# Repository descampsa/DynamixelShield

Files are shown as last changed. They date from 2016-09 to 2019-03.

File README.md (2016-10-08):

# Dynamixel shield

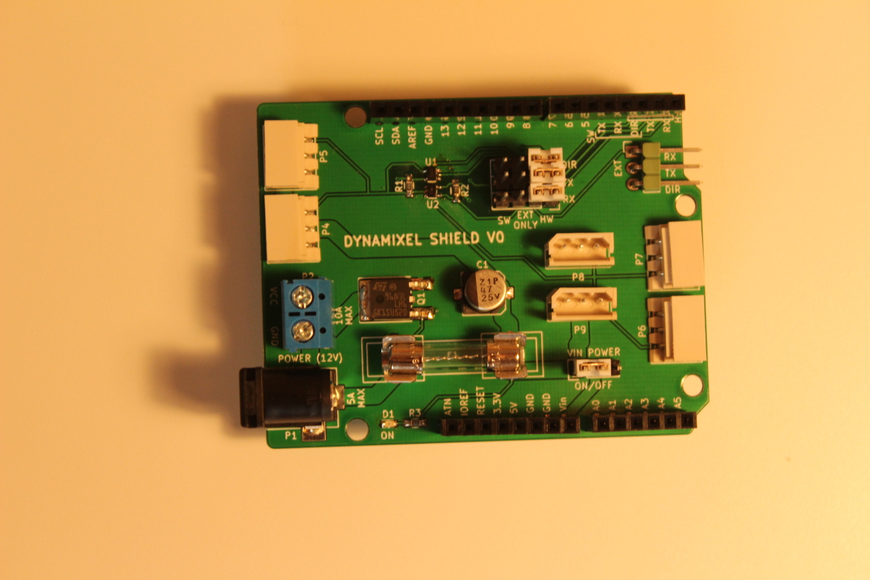
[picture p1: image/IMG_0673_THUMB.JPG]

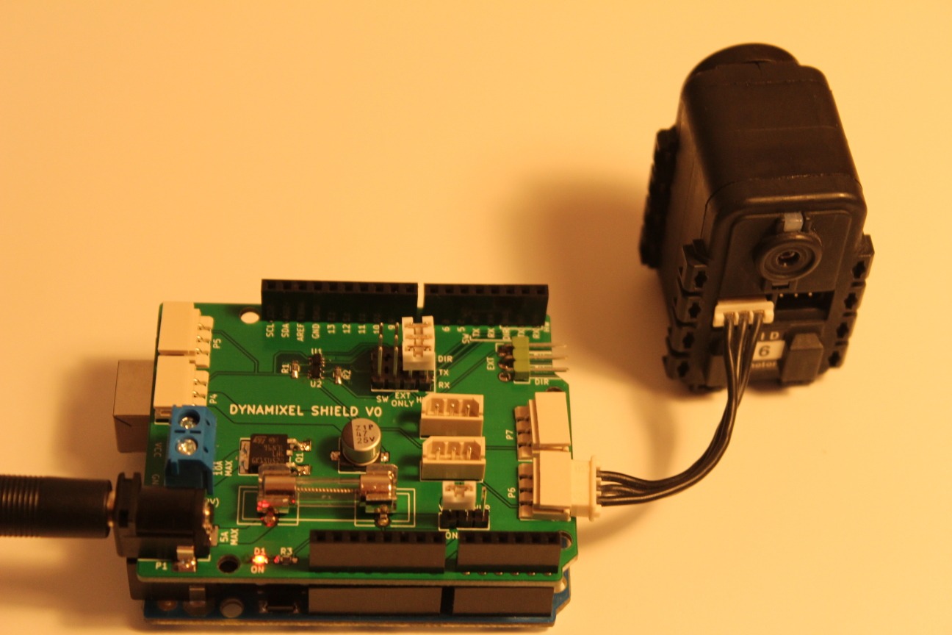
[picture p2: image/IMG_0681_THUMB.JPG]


## What is it?

This is an arduino shield to control dynamixel servo motors from Robotis. AX and MX series (TTL version) are supported. Thanks to their half-duplex serial control protocol, you can chain them and control a lot of motor simultaneously (up to 254 in theory). It is possible to control those motors with an arduino without additionnal hardware, but this board makes it easier and cleaner.

## How to use it?

### Hello world (aka blink my led)

First install the [ardyno](https://github.com/descampsa/ardyno/) library, using the Arduino Library Manager, or directly from the github repository.
Then open the "test_led" example and upload it. The shield can not be installed when you install the program.
Install the shield, check that the jumpers are on 'HW' position, connect the motor and a 12v power supply, and voila, the motor "led" should start blinking!
To get the motor moving (that's the point, after all), check the "test_motor" exemple. The documentation is still lacking, but by browsing examples and code, you should be able to do understand how it works. If you have any question, just ask.

### Software serial

The default mode explained above is to use the first hardware UART (Serial) of the board to communicate with the motors. This has the advantage that you can usethe full communication speed (up to 2Mbaud, by default 1Mbaud) of the protocol. However, boards that only have one hardaware uart (e.g. Uno), that means that you can't simultaneously use the USB port to communicate with the external world, since it also uses this UART. If you want to do that, you have to use the SoftwareSerial mode. The disadvantage is that you are limited to low baud rates (check the SoftwareSerial library documentation). You will have to change the baud rate of the motor using the hardware serial before (see "test_speed" example).

To use the SoftwareSerial mode, change the jumper to 'SW' position, and replace the line
```
HardwareDynamixelInterface interface(Serial,2);
```
by

```
SoftwareDynamixelInterface interface(4,3,2);
```

The first version take the hardware serial instance, and the direction pin as parameters, while the second one take rx pin, tx pin and direction pin.

### Other Hardware Serial

For boards that have multiple hardware uart, you may use any of those ports by connecting the corresponding pins to the 'EXT' connector. Just set the jumper to 'EXT ONLY' position, and connect RX/TX/DIR pins to the rx/tx pins of the uart and the direction pin configured in your code.

## Which boards are compatible?

Most of the code is platform independent, but it has only been tested with AVR boards. If you want to use another platform and find a bug, open an issue in ardyno repository.
The shield supports both 5V and 3.3V boards.

I also successfully tested it with the Arduino 101, but there are still a few shortcomings in the serial libray of this board, so this is experimental.

## Great, how do i get one?

The good news is that all is open source, the kicad project, gerber file, code, bom, all you need to make your own. Gerber and bom are also available on [kitnic](kitnic.it), where you may order the parts very easily. The bad news is that you can't buy one, i do not sell it for now.
I have a few unpopulated pcb left, however, so if you are interested, just ask and i will send you one for shipping cost.

## Warning

This board is functionnal, but has not yet been tested extensively, especially for high loads. Make sure you know what you are doing if you use it.

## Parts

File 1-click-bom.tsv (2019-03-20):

References | Qty | Description | Manufacturer | MPN | Digikey | Mouser | RS | Newark | Farnell
Q1 | 1 | MOSFET N TO-252-2Lead | ON semiconductor | NTD4904NT4G | NTD4904NT4GOSCT-ND | 863NTD4904NT4G
F1 | 2 | F Small Fuse Fuseholder5x20 horiz lateral | Littelfuse | 01110501Z | F4189-ND | 57601110501Z |  | 69R7705 | 1848686
F1_10A | 1 | Fuse 5x20 10A | Littelfuse | 5ST 10-R | 507-1256-ND | 5305ST10R
F1_5A | 1 | Fuse 5x20 5A | Littelfuse | 5ST 5-R | 507-1253-ND | 5305ST5R
P1 | 1 | BARREL JACK DC Barrel Jack | CUI Inc. | PJ-102AH | CP-102AH-ND | 490PJ102AH
P2 | 1 | CONN 01X02 Connector 01x02 bornier2 5.08mm | TE Connectivity | 1776493-2 | A122765-ND | 57117764932 |  | 95Y9029
U1 | 1 | 74AHCT1G126 SOT-353 | Diodes Incorporated | 74AHCT1G126SE-7 | 74AHCT1G126SE-7DICT-ND | 62174AHCT1G126SE7 |  |  | 2057393
U2 | 1 | 74AHC1G125 SOT-353 | Diodes Incorporated | 74AHC1G125SE-7 | 74AHC1G125SE-7DICT-ND | 62174AHC1G125SE7 |  | 47T3881 | 1893809
C1,C2 | 1 | CP 220uF Polarised capacitor c elec 6.3x7.7 25V 20% | Panasonic | EEE-FTE221XAP | PCE5009CT-ND | 667EEEFTE221XAP |  | 29AC5209 | 2284803
R1,R2,R3,R4,R6 | 5 | R 10K Resistor 0603 | Panasonic | ERJ-3GEYJ103V | P10KGDKR-ND | 667ERJ3GEYJ103V | 7325656 | 97W7470 | 2059627
R5 | 1 | R 200 Resistor 0603 | Panasonic | ERJ-3GEYJ201V | P200GCT-ND | 667ERJ3GEYJ201V | 7325769 | 65T8597 | 2059582
D1 | 1 | LED 0603 Red | OSRAM Opto Semiconductors | LS Q976-NR-1 | 475-2512-1-ND | 720LSQ976NR1
P3 | 1 | CONN 01X03 Connector 01x03 Pin Header Angled 1x03 2.54mm | Molex | 22-28-8030 | WM50013-03-ND | 53822288030 |  | 91M6511
P4,P5,P6,P7 | 4 | CONN 01X03 Connector 01x03 Molex spox 1x3 right 2.5mm | Molex | 22-05-7035 | WM18901-ND | 53822057035 | 6878095 | 57R9151
P8,P9 | 2 | CONN 01X03 Connector 01x03 Molex spox 1x3 straight 2.5mm | Molex | 22-03-5035 | WM18887-ND | 53822035035 | 6878048 | 98K6552 | 9979620
JP1,JP2,JP3 | 3 | JUMPER4 Pin Header Straight 1x04 2.54mm | Molex | 22-28-4030 | WM50014-03-ND | 53822284030 |  | 56H1960
JP4 | 1 | JUMPER3 Pin Header Straight 1x03 2.54mm | Molex | 22-28-4040 | WM50014-04-ND | 53822284040 |  | 29X1962 | 2381172
JP1_,JP2_,JP3_,JP4_ | 4 | SHUNT 1x2 2.54mm | Amphenol FCI | 68786-102LF | 609-3121-ND | 64968786102LF |  | 53K1469 | 2579771
SHIELD1 | 1 | Arduino Shield stacking headers for Arduino (R3 Compatible) | Adafruit |  | 1528-1074-ND | 48585

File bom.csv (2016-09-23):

DYNAMIXEL_SHIELD
N° Mouser | N° de fab. | Fabricant | Description | RoHS | Cycle de vie | Qté. | Prix (EUR) | Poste: (EUR)
511-STD96N3LLH6 | STD96N3LLH6 | STMicroelectronics | MOSFET N-Ch 30V 0.0037 Ohm 80A STripFET VI | RoHS : conforme |  | 1 | € 0,679 | € 0,68
621-74AHCT1G126SE-7 | 74AHCT1G126SE-7 | Diodes Incorporated | Tampons et circuits d’excitation AHC TTL Compatible LOGIC | RoHS : conforme |  | 1 | € 0,22 | € 0,22
621-74AHC1G125SE-7 | 74AHC1G125SE-7 | Diodes Incorporated | Tampons et circuits d’excitation SINGLE NON INVERTING DRIVER 3-STATE | RoHS : conforme |  | 1 | € 0,256 | € 0,26
576-01110501Z | 01110501Z | Littelfuse | Mâchoires ACS 2AG PC MNT CLIP | RoHS : conforme |  | 2 | € 0,109 | € 0,22
530-5ST10-R | 5ST 10-R | Bel | Fusibles à cartouche Fuse | RoHS : conforme |  | 1 | € 0,192 | € 0,19
538-22-03-5035 | 22-03-5035 | Molex | Embases et logements de câbles 2.5 VERT HDR SPOX 3P shrouded | RoHS : conforme |  | 2 | € 0,443 | € 0,89
538-22-05-7035 | 22-05-7035 | Molex | Embases et logements de câbles 3 CKT 2.5MM R/A HDR | RoHS : conforme |  | 4 | € 0,471 | € 1,88
490-PJ-102AH | PJ-102AH | CUI Inc. | Connecteurs d'alimentation continue Power Jacks | RoHS : conforme | Nouveau chez Mouser | 1 | € 1,08 | € 1,08
667-ERJ-3GEYJ103V | ERJ-3GEYJ103V | Panasonic | Résistances à couches épaisses - CMS 0603 10Kohms 5% AEC-Q200 | Conforme à RoHS par dispense |  | 3 | € 0,091 | € 0,27
630-HSMC-C130 | HSMC-C130 | Broadcom Limited | DEL standard - CMS Red Thin Profile 155lm | RoHS : conforme |  | 1 | € 0,08 | € 0,08
649-68786-102LF | 68786-102LF | FCI / Amphenol | Embases et logements de câbles SHUNT 15u" GOLD | RoHS : conforme |  | 4 | € 0,172 | € 0,69
485-85 | 85 | Adafruit | Accessoires Adafruit Shield stacking headers for Arduino (R3 Compatible) | RoHS : conforme |  | 1 | € 1,76 | € 1,76
571-1776493-2 | 1776493-2 | TE Connectivity | Borniers fixes SIDE WIRE ENTRY TB 5.08MM BL | RoHS : conforme |  | 1 | € 0,31 | € 0,31
530-5VT5-R | 5VT 5 -R | Bel | Fusibles à cartouche | RoHS : conforme |  | 1 | € 0,183 | € 0,18
647-UWT1E470MCL6S | UWT1E470MCL6GS | Nichicon | Condensateurs électrolytiques en aluminium - CMS 25volts 47uF 6.3x5.8 20% | RoHS : conforme |  | 1 | € 0,284 | € 0,28
571-826947-3 | 826947-3 | TE Connectivity | Embases et logements de câbles 2X03 POS VERT TIN | RoHS : conforme |  | 1 | € 0,188 | € 0,19
571-4-103321-5 | 4-103321-5 | TE Connectivity | Embases et logements de câbles 03 MODII HDR SRST B/A .100CL | RoHS : conforme |  | 1 | € 0,094 | € 0,09
571-5-146274-4 | 5-146274-4 | TE Connectivity | Embases et logements de câbles 4P HEADER TIN single row | RoHS : conforme |  | 3 | € 0,16 | € 0,48

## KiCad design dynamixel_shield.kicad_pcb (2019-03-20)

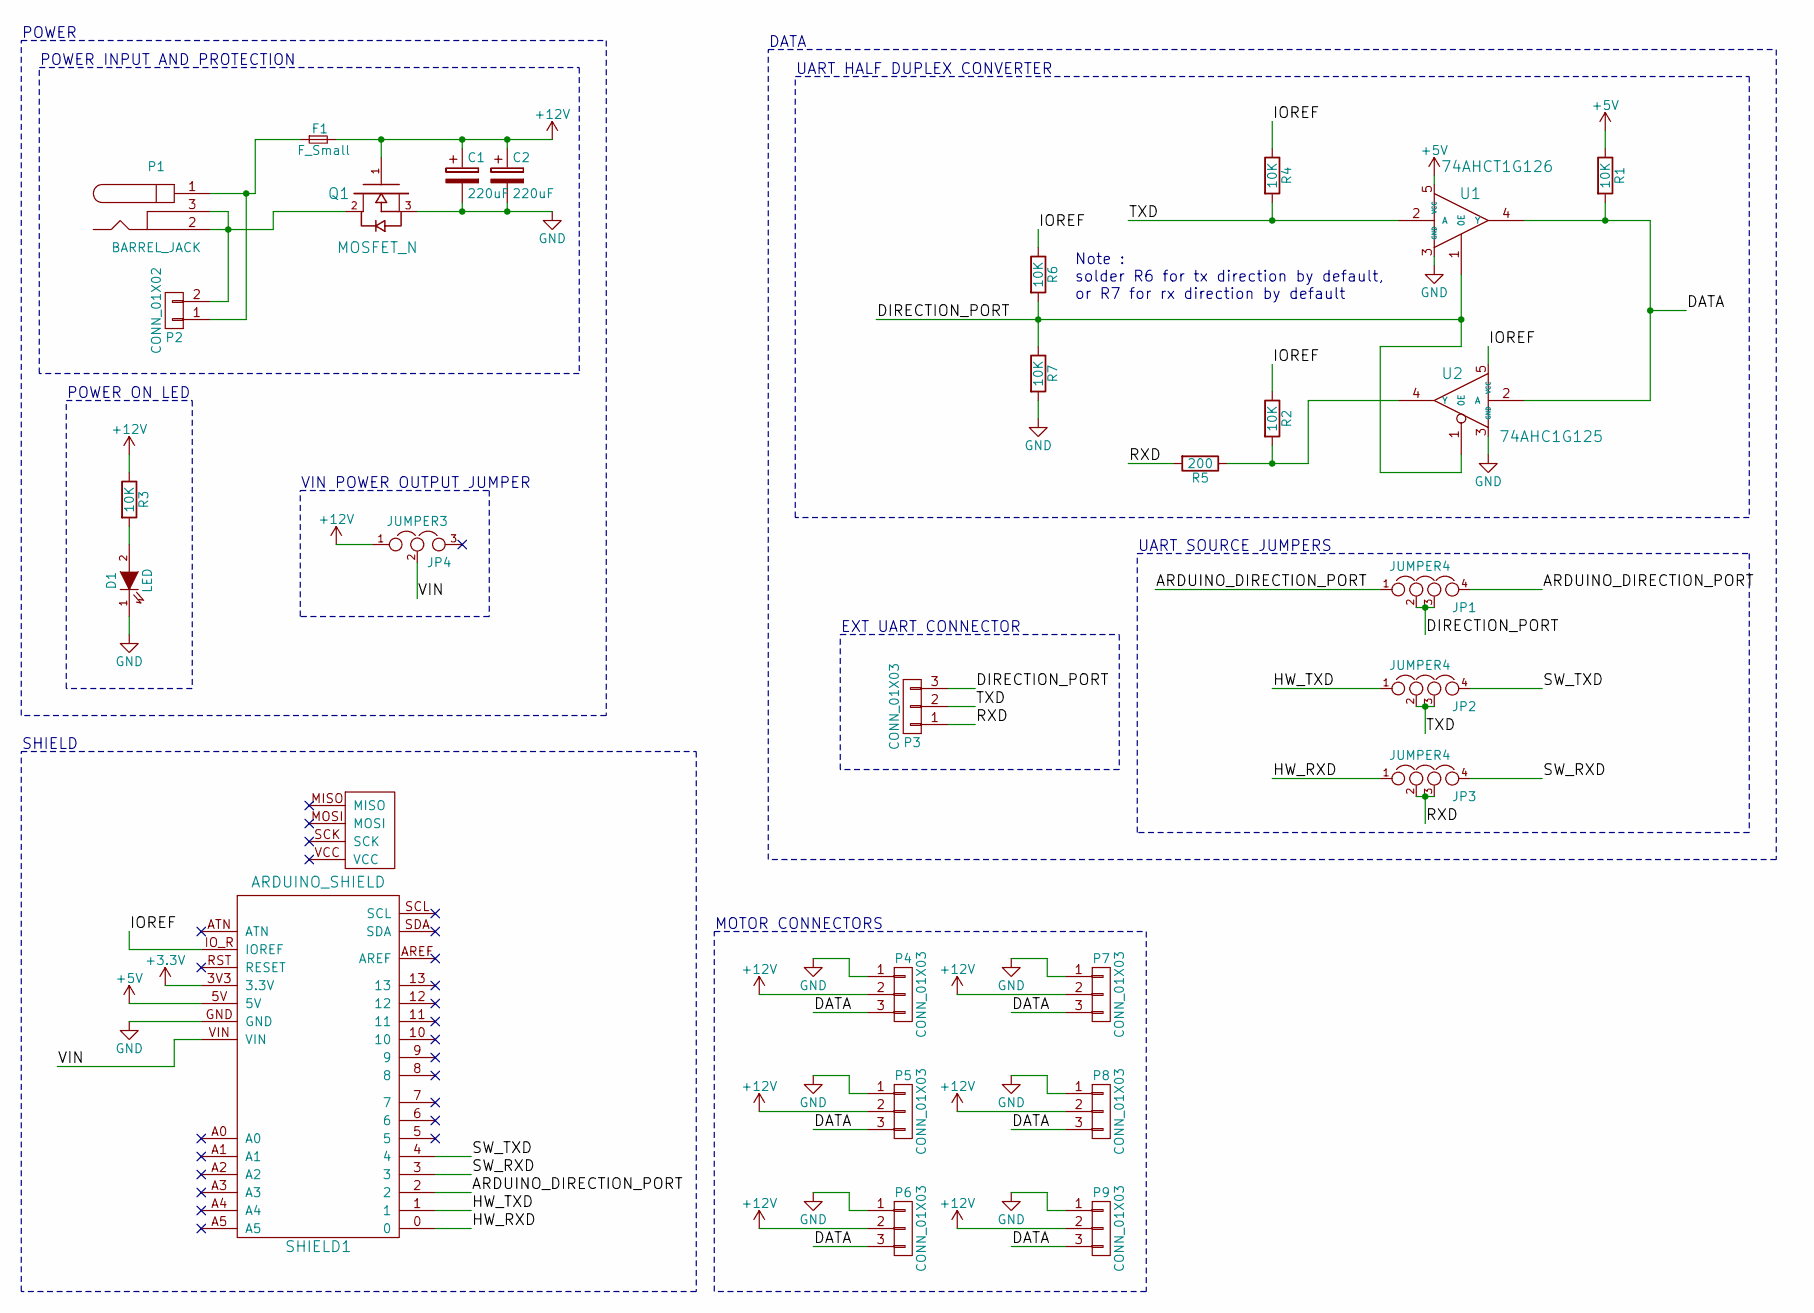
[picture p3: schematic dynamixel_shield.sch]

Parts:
C1, C2: 220uF; CP_Elec_6.3x7.7
D1: LED; LED_0603
F1: F_Small; Fuseholder5x20_horiz_lateral
JP1, JP2, JP3: JUMPER4; Pin_Header_Straight_1x04
JP4: JUMPER3; Pin_Header_Straight_1x03
P1: BARREL_JACK
P2: CONN_01X02; bornier2
P3: CONN_01X03; Pin_Header_Angled_1x03
P4, P5, P6, P7: CONN_01X03; Molex_spox_1x3_right
P8, P9: CONN_01X03; Molex_spox_1x3_straight
Q1: MOSFET_N; TO-252-2Lead
R1, R2, R3, R4, R6, R7: 10K; R_0603_HandSoldering
R5: 200; R_0603_HandSoldering
SHIELD1: ARDUINO_SHIELD; Arduino_shield_dynamixel
U1: 74AHCT1G126; SOT-353
U2: 74AHC1G125; SOT-353

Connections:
+3V3: SHIELD1.3V3 (3.3V)
+5V: R1.1, SHIELD1.5V, U1.5 (VCC)
+12V: C1.1, C2.1, F1.2, JP4.1, P4.2, P5.2, P6.2, P7.2, P8.2, P9.2, Q1.1 (G), R3.1
/ARDUINO_DIRECTION_PORT: JP1.1, JP1.4, SHIELD1.2
/DATA: P4.3, P5.3, P6.3, P7.3, P8.3, P9.3, R1.2, U1.4 (Y), U2.2 (A)
/DIRECTION_PORT: JP1.2, JP1.3, P3.3, R6.2, R7.1, U1.1 (0E), U2.1 (0E)
/HW_RXD: JP3.1, SHIELD1.0
/HW_TXD: JP2.1, SHIELD1.1
/IOREF: R2.1, R4.1, R6.1, SHIELD1.IO_R (IOREF), U2.5 (VCC)
/RXD: JP3.2, JP3.3, P3.1, R5.2
/SW_RXD: JP3.4, SHIELD1.3
/SW_TXD: JP2.4, SHIELD1.4
/TXD: JP2.2, JP2.3, P3.2, R4.2, U1.2 (A)
/VIN: JP4.2, SHIELD1.VIN
GND: C1.2, C2.2, D1.1 (K), P4.1, P5.1, P6.1, P7.1, P8.1, P9.1, Q1.3 (S), R7.2, SHIELD1.GND, U1.3 (GND), U2.3 (GND)
unnamed: D1.2 (A), R3.2
unnamed: F1.1, P1.1, P2.1
unnamed: P1.2, P1.3, P2.2, Q1.2 (D)
unnamed: R2.2, R5.1, U2.4 (Y)

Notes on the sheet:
POWER INPUT AND PROTECTION
UART HALF DUPLEX CONVERTER
MOTOR CONNECTORS
POWER ON LED
SHIELD
EXT UART CONNECTOR
UART SOURCE JUMPERS
VIN POWER OUTPUT JUMPER
POWER
DATA
Note : solder R6 for tx direction by default, or R7 for rx direction by default

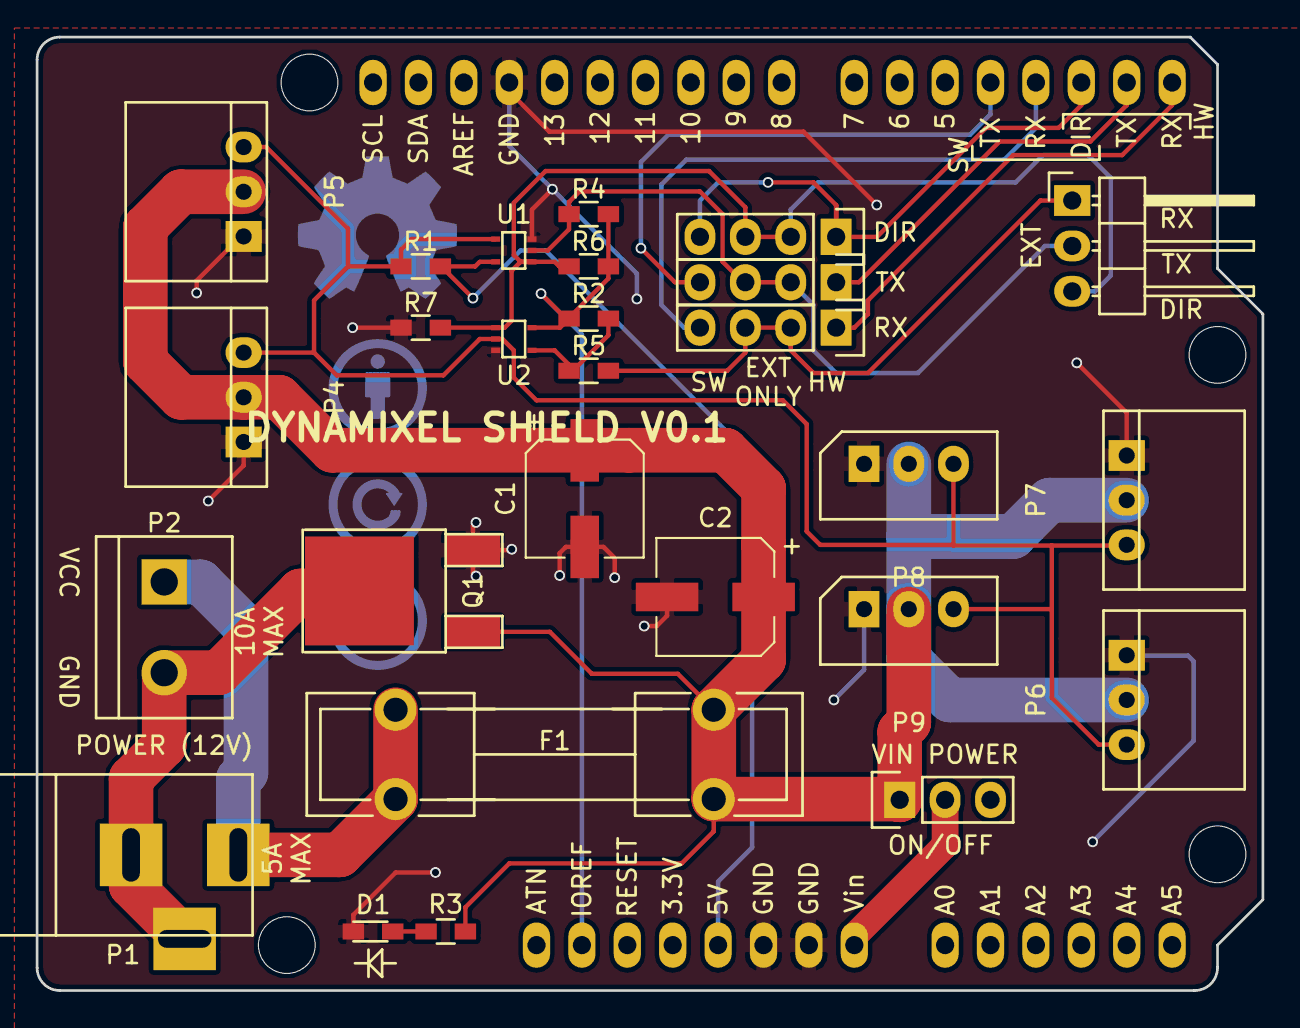
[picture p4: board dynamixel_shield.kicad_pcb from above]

Board: 2 copper layers, 68.6 x 53.3 mm, 28 parts (0 on the bottom side), 18 nets.

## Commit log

2016-08-24 Update silkscreen
    [dynamixel_shield.kicad_pcb]
2016-08-24 Add power on LED
    [dynamixel_shield.kicad_pcb, dynamixel_shield.sch]
2016-08-24 Fix error in schematics
    Arduino direction port was not connected in the SW configuration.
    [dynamixel_shield.kicad_pcb, dynamixel_shield.sch]
2016-08-26 move ext connector to make place for the fourth mounting hole
    [dynamixel_shield.kicad_pcb, dynamixel_shield.sch]
2016-09-07 add annotation to the schematic
    [dynamixel_shield.sch]
2016-09-23 add bom from mouser
    [bom.csv]
2016-10-01 add gerber files
    [dynamixel_shield.GBL, dynamixel_shield.GBO, dynamixel_shield.GBS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]
2016-10-01 add 1 click bom (from mouser bom)
    [1-click-bom.tsv]
2016-10-01 add mouser number for arduino header, appears to work for digikey too
    [1-click-bom.tsv]
2016-10-02 complete 1-click-bom with suppliers part numbers (only mouser and digikey are sane)
    [1-click-bom.tsv]
2016-10-02 remove quoting, for nicer github display
    [1-click-bom.tsv]
2016-10-02 change capacitor height (bom related only, footprint is the same)
    [dynamixel_shield.kicad_pcb, dynamixel_shield.sch]
2016-10-02 fix description fields in 1-click_bom using kicad export script (at least it is in english now ...)
    [1-click-bom.tsv]
2016-10-02 update bom with more available parts
    [1-click-bom.tsv]
2016-10-02 remove nonsensical parts from autocomplete
    [1-click-bom.tsv]
2016-10-02 fix some newark part numbers
    [1-click-bom.tsv]
2016-10-09 fix a few shortcomings of the pcb, thanks to tautech from eevblog forum
    remove potential acid trap between p8 and p9
    increase pad size of molex connectors
    move polarity indicators to be visible
    increase led pad size for easier soldering
    [dynamixel_shield.kicad_pcb]
2016-10-09 put the fuse before the reverse voltage protection (thanks to bktemp from eevblog forum)
    Quoting bktemp user on eevblog:
    When the fuse fails, there will be a voltage spike.
    Since there is no load except the mosfet gate, the voltage spike will damage the mosfet,
    maybe even shorting gate-source and therefore the input supply.
    If the gate is connected after the fuse, is will be connected in parallel with C1,
    providing some protection for the sensitive gate.
    [dynamixel_shield.kicad_pcb, dynamixel_shield.sch]
2016-10-10 add a few vias between ground planes (suggested by bson from eevblog)
    [dynamixel_shield.kicad_pcb]
2016-10-10 add small traces to vias, so that they are not disconnected when you refill the ground zones
    [dynamixel_shield.kicad_pcb]
2016-10-13 remove vias in ground plane
    [dynamixel_shield.kicad_pcb]
2016-10-13 add pull up and protection resistor on uart lines
    [dynamixel_shield.sch]
2016-10-15 add optional resistor to set default direction in either rx or tx
    [dynamixel_shield.sch]
2016-10-15 update pcb with new resistors
    [dynamixel_shield.kicad_pcb, dynamixel_shield.sch]
2016-10-15 slightly update arduino silkscreen to be visible behind headers
    [dynamixel_shield.kicad_pcb]
2016-10-15 move footprints to separate github repositories
2016-10-31 add a few vias between ground planes
    [dynamixel_shield.kicad_pcb]
2016-10-31 update resistor value
    [dynamixel_shield.sch]
2016-10-31 update bom with new parts
    [1-click-bom.tsv]
2019-03-19 tweak some components placement
    [dynamixel_shield.kicad_pcb, dynamixel_shield.sch]
2019-03-20 increase capacitors, add a few vias
    [dynamixel_shield.kicad_pcb, dynamixel_shield.sch]
2019-03-20 update bom
    [1-click-bom.tsv]
